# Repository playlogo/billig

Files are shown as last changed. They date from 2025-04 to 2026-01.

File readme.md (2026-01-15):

# Billig - A 3D printer from scratch

Flyby

> *Designing a 3D printer from scratch in 5 days*

**Bom**: [Google sheets](https://docs.google.com/spreadsheets/d/1451xPwitG2cd0BywjLuyT1Flae_F1tCVU7JKSqZtRoc/edit?usp=sharing)  
**CAD**: [Onshape](https://cad.onshape.com/documents/d0a1f0aa5ccbfda89a60ed00/w/724bd13dc87be16ac72aafeb/e/c63896b50a2324a549602fe6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)

About the printer:

- 440x230x200mm printing volume
- 940x410x465mm frame
- Reuses a lot of parts from two "broken" [Anycubic Kobra 2 Neos](https://de.anycubic.com/products/kobra-2-neo)
- Direct drive extruder & dual 5020 part cooling
- Completely enclosed electronics
- Build-in ABL
- With a rpi zero & Klipper-Ready
- ~$500 (including the two broken printers)

Take a look at the [Journal (has lot's of pictures!)](JOURNAL.md), the [Design notes](notes.md) or the [custom PCB (that didn't make it)](pcb/readme.md)!

Note: The stls in `printer/stls/` are only for my reference, export & download the latest ones form Onshape!

## Roadmap

Use Elecrow 7.0" Esp32 Touch display as an interface for klipper.

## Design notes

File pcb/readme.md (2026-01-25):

# Kontakt - Fan & LED control board

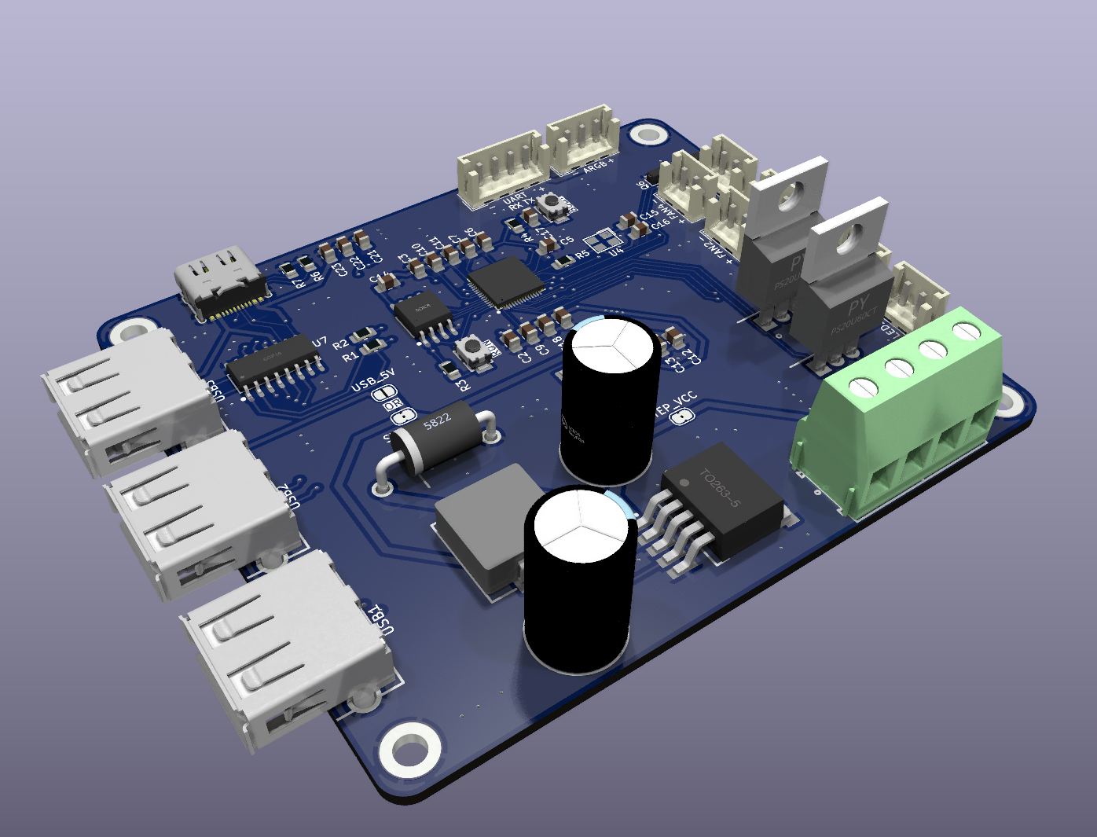
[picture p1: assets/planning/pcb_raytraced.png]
PCB routing
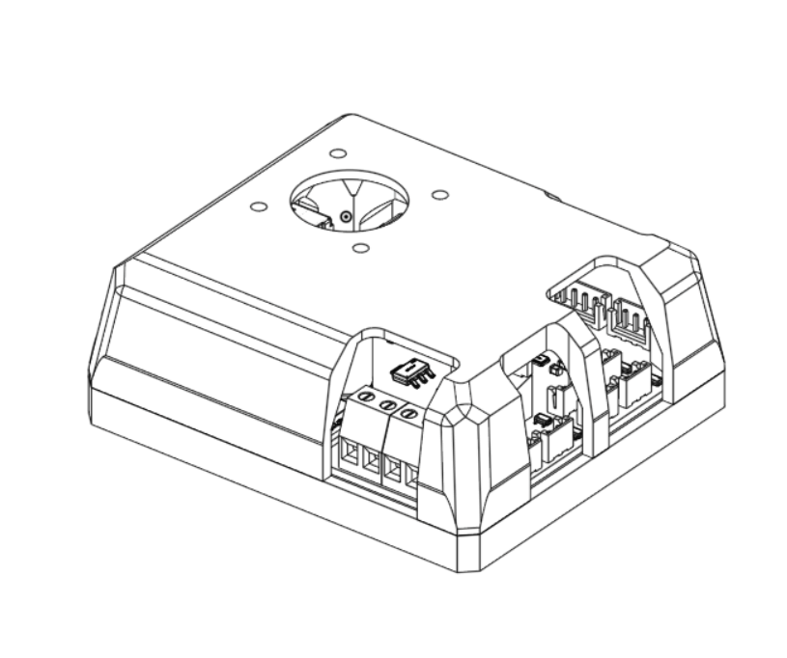
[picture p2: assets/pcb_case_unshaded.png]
PCB components
|  | |
| ---|---|
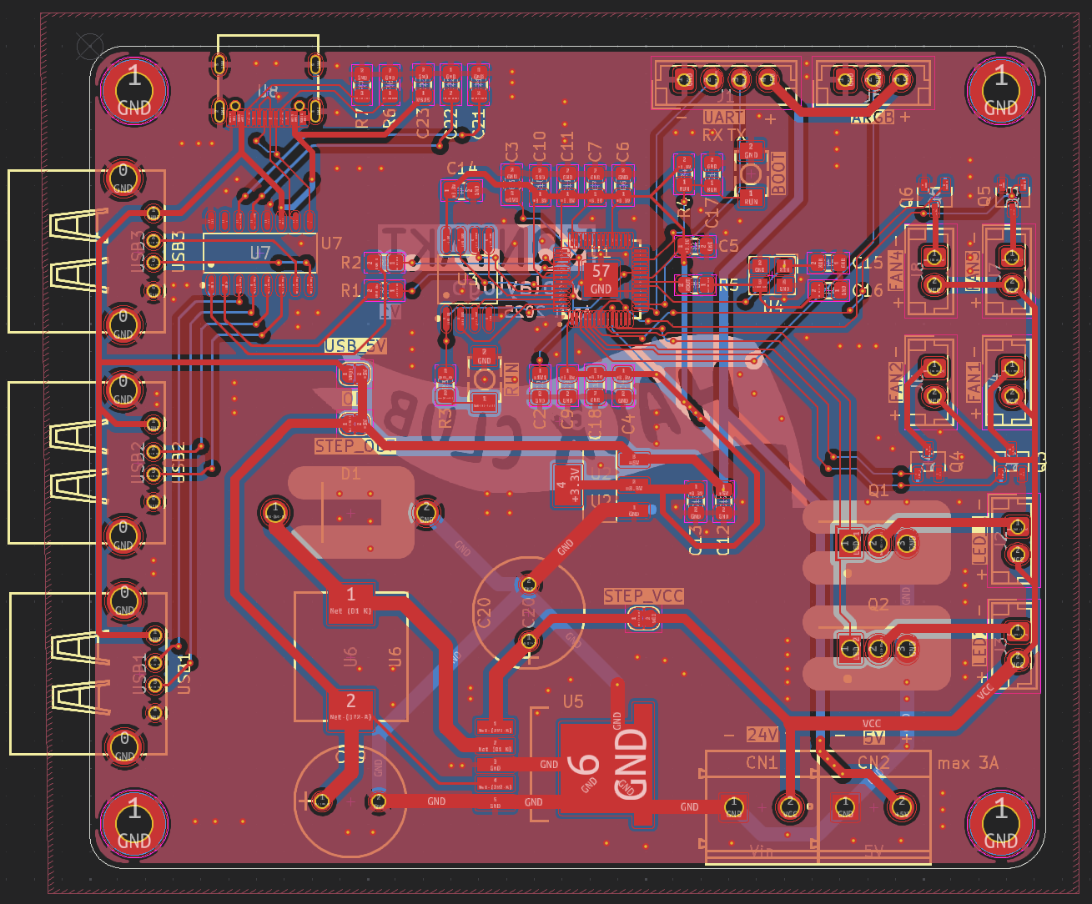
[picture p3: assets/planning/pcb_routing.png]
Case render
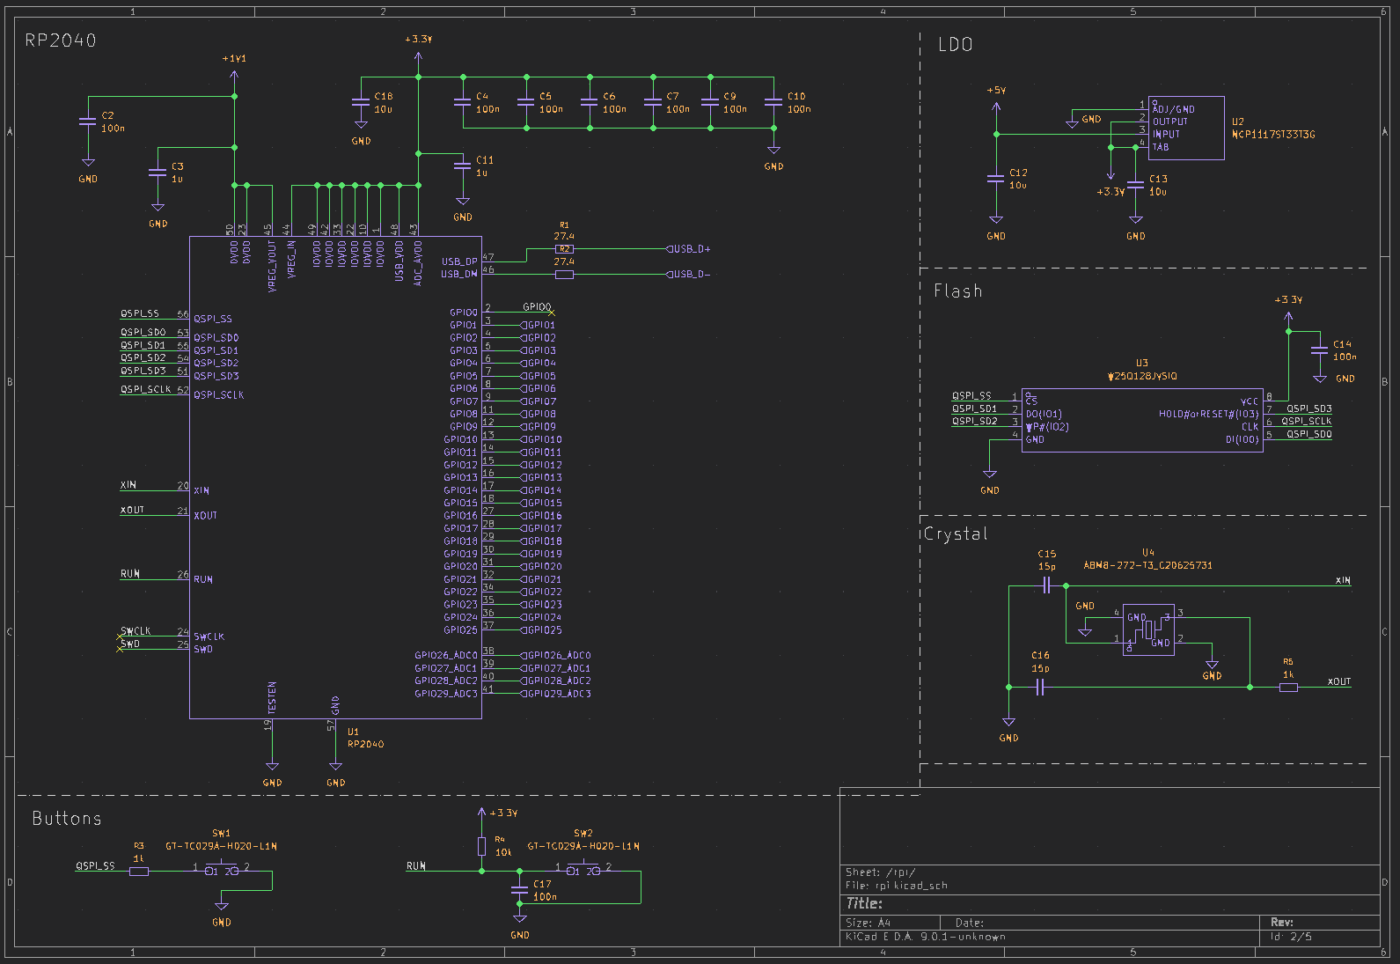
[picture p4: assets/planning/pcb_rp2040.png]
Case side view
|  |  |

Features:

- 24V power input
- Build-in 5V 3A Stepdown (for RP2040 and external RPI)
- RP2040 with 128MB Flash
- 3 Port USB hub
- 1x UART connection
- 1x ARGB connection
- 2x High current 24V PWM outputs (5A)
- 4x Low current 24V PWM outputs (2A)
- [A 3D printable case](case/) with an included 30mm fan, can be mounted to a DIN rail with [this adapter](https://www.printables.com/model/259120-horizontal-ssr-din-rail-mount/files)

Why ?: I originally only wanted to slap a rpi pico onto a pcb and add 6 mosfets to it, but like you can see I got sidetracked and added my own rp2040 (my first one!), a step-down converter (also a first) and a USB hub...

It'll be used to control the fans inside the electronics enclosure and connect the 2 control boards to the one usb port of the RPI Zero 2w, which it will also power. The high current PWM outputs are for eventual LED bar upgrades, which might or might not happen.

Firmware: I'll be using Klipper on the RP2040 with [this extension module](https://github.com/julianschill/klipper-led_effect) to control the Neopixel

Schematic: [Here](../files/schematic.pdf)

Libraries:

- [easyeda2kicad](https://github.com/uPesy/easyeda2kicad.py), needs to be installed separately, used for downloading LCSC schematics & footprints
  - Run `easyeda2kicad --full --lcsc_id=<id>` to download each component (one-by-one, yes...)

## Components

LCSC IDs:

- C2040 - RP2040
- C26537 - LDO
- C778164 - 2x Button
- C113767 - SPI Flash
- C20625731 - Crystal
- C7429053 - High current mosfet
- C5364313 - Low current mosfet
- C10002 - LM2596 3A Step down - [datasheet](https://www.lcsc.com/datasheet/lcsc_datasheet_2410010301_Texas-Instruments-LM2596SX-5-0-NOPB_C10002.pdf)
  - L1: 47uH L39 - C7529419
  - Cout: 330uF/35V - C242140
  - D1: C7503125
  - Cin: 680uF/35V - C178718
- C2915639 - Screw terminal
- C2988369 - USB C Female connector
- C192893 - USB Hub chip
- C503996 - USB Female plug

Resistors & Capacitors

- 10K C5140188
- 5.1k C26023
- 1k C17513
- 27.4ohm C2079437

- 100nF C29926
- 1uF C541528
- 10uF C1713
- 15pF C5186731

## BOM

### Parts

> Note: This is my first time soldering a rp2040 (QFN-* package in general) :D

| LCSC ID | Name | Amount |
|---|---|---|
| C2040 | RP2040 | 1x |
| C26537 | LDO | MOQ (5) |
| C778164 | 2x Button | MOQ (5) |
| C113767 | SPI Flash | 1x |
| C20625731 | Crystal | 1x |
| C7429053  | High current mosfet | 2x |
| C5364313  | Low current mosfet | MOQ(10) |
| C10002 | LM2596 3A Step down | 1x |
| C7529419  | LM2596 3A Step down (L1) | 1x |
| C242140 | LM2596 3A Step down (Cout) | MOQ (5) |
| C7503125  | LM2596 3A Step down (D1) | MOQ (5) |
| C178718 | LM2596 3A Step down (Cin) | 1x |
| C2915639  | Screw terminal | MOQ (5) |
| C2988369  | USB C Female connector | MOQ (5) |
| C192893 | USB Hub chip | MOQ (5) |
| C503996 | USB Female plug | MOQ (10) |
| C5140188  | 10K | MOQ (100) |
| C26023 | 5.1k | MOQ (100) |
| C17513 | 1k | MOQ (100) |
| C2079437  | 27.4ohm | MOQ(50) |  
| C29926 | 100nF | MOQ(50) |
| C541528 | 1uF | MOQ(50) |
| C1713 | 10uF | MOQ(20) |
| C5186731  | 15pF | MOQ(100) |

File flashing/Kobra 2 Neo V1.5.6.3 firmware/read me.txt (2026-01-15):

Update steps:
1. Format the TF card, copy the Motherboard firmware (firmware.bin) to the root directory of the TF card, and only store this file in the TF card.

2. Insert the TF card into the printer in the shutdown state, and then turn on the printer.

3. Wait for a while, and automatically update the firmware in the black screen state.

4. After the update is completed, the screen will appear  “Anycubic LOGO”, and then automatically enter the main interface. Then shut down and pull out the SD card. update completed.

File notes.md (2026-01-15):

# Design notes

Contents:

- [Filament holder](#filament-holder)
- [Bed mount](#bed-mount)
- [Frame - Bottom corner pieces](#frame---bottom-corner-pieces)
- [Frame - TPU feet](#frame---tpu-feet)
- [Motion - Endstops](#motion---endstops)
- [Frame - Z-Lead screw bottom assembly](#frame---z-leadscrew-bottom-mount)
- [BOM - Screws etc](#bom---screws-etc)
- [BOM - Reuse of parts from Kobras](#bom---reuse-of-parts-from-kobras)
- [Electronics - Mains wiring](#electronics---mains-wiring)
- [Electronics - 2 MBs](#electronics---2-controller-boards--mbs)
- [Electronics - Toolhead breakout board](#electronics---toolhead-breakout-board)
- [Electronics - Original screen](#electronics---original-screen)

## Filament holder

I'll reuse the original "Filament clip-on holder". I've added a PTFE tube mount to the top of the printer to guide the filament over the top edge and into the printing area:

*I'll add a leftover PTFE tube to the purple section*

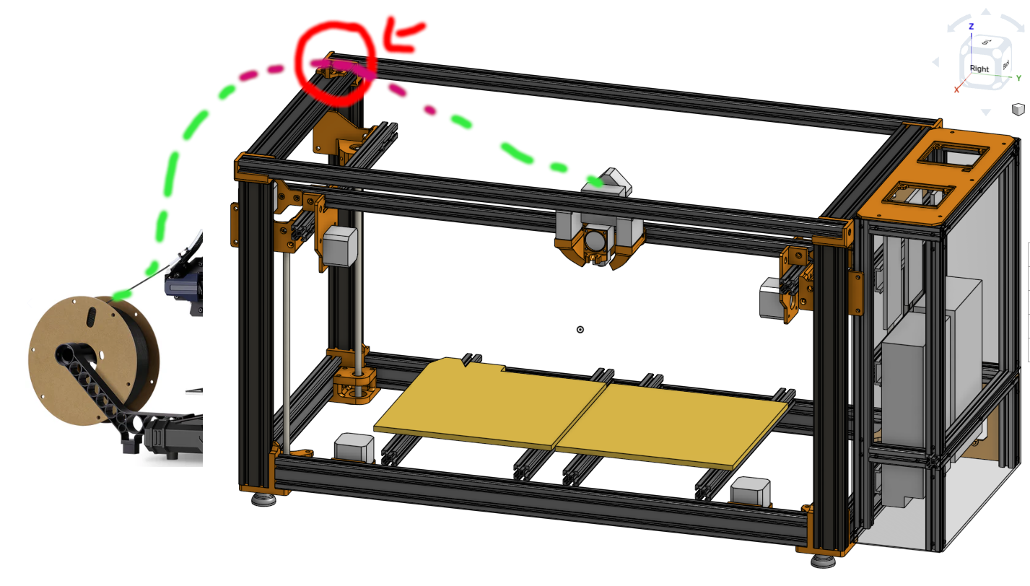
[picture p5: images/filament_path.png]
Filament path


## Bed mount

The two heatbeds will be mounted to the vertical aluminum extrusions using the silicon bed spacers, and the vertical extrusions will be mounted to the frame using these 90deg brackets (inspired by the voron 2.4 bed mount, since it can hold the sold aluminum bed, it should be strong enough to hold the cheap pcb heatbed)

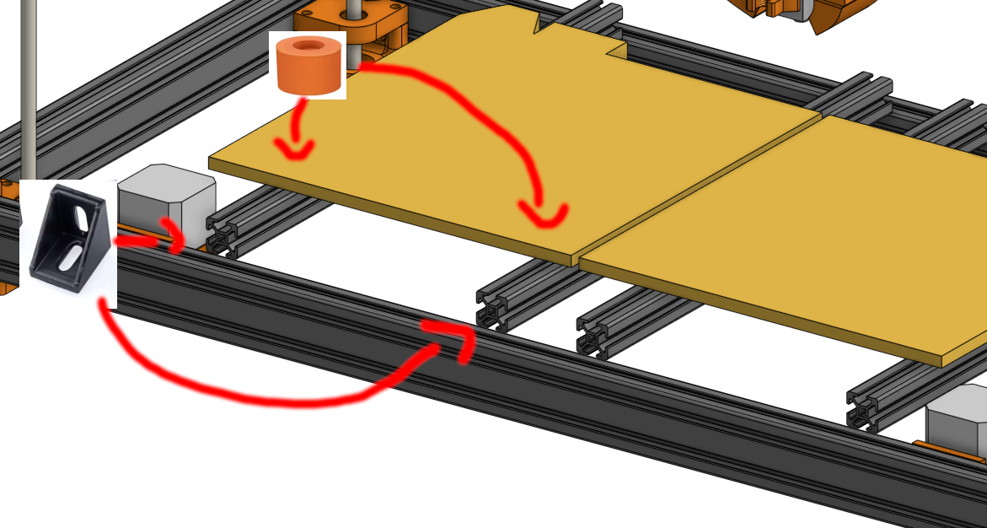
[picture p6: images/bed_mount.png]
Bed mount


## Frame - Bottom corner pieces

The aluminum extrusions will be mounted to the corner pieces using [blind joints](https://docs.vzbot.org/assets/images/manual/blind-joints/blind-joints.png). Additionally the vertical extrusions are being reused from the Kobra printers, and "slide" into the corner pieces (see picture).

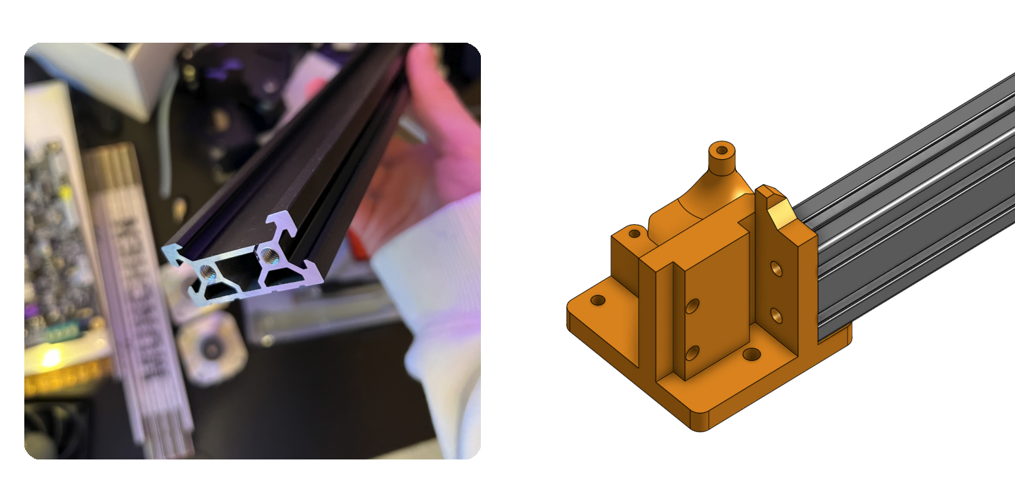
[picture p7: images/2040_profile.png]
2040 Profile


## Frame - TPU feet

The feet will be printed with TPU to be flexible and absorb *some* of the vibrations. They'll be screwed into the bottom corner pieces using M5 Screws

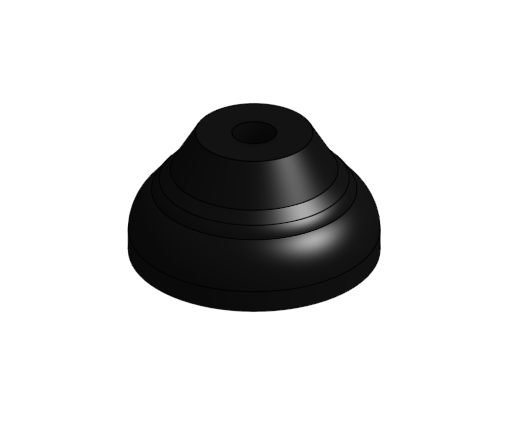
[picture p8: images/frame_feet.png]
Feet


## Motion - Endstops

I'll use microswitches as X and dual Y endstops. The Z-Axis will use the ABL sensor. Since I didn't find any accurate measurements of the microswitches, I made the "activator/clicker" (marked in green) a separate part to be easelly modified.

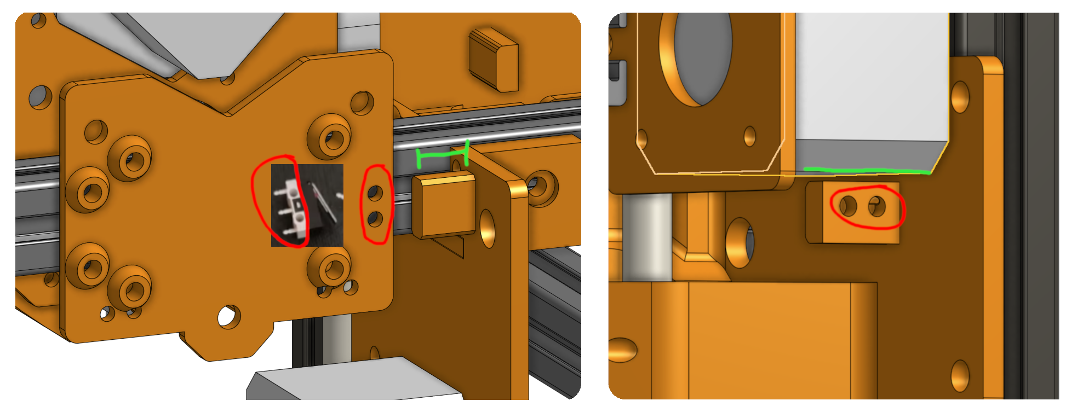
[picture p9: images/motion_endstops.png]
Endstops


## Frame - Z-Leadscrew bottom mount

Stackup of the bottom assembly:

- Printed top-cover part
- 608 barring
- Printed Spacer
- GT 40T pulley
- 608 barring
- Printed bottom part

## BOM - Screws, etc

I have various screws and other stuff left over from the two Kobra printers and the Ender3NG I just build. The BOM only contains the fasteners I'm personally missing to build the printer, not all the required ones to build it from scratch!

## BOM - Reuse of parts from Kobras

This printer reuses various parts from the two Anycubic Kobras. Most notably:

- Heatbeds & Buildplate
- PSUs, MBs, Motors, some Belts, Leadscrew
- Direct drive extruder, Hotend, ABL probe, Wires
- Some aluminum extrusions (all the darker ones in the CAD model are reused)

I **do not** reuse:

- Metal structural parts (plates, etc)
- Plastic structural parts

All orange parts in the CAD modal are self designed and will be 3D printed!

## Electronics - Mains wiring

I'll reuse the mains cable socket with buildin fuse from one of the kobras. I'll then use [this thing:5018395](https://www.thingiverse.com/thing:5018395) to mount 3 Wago 221 connectors to split the incomming mains for the two PSUs.

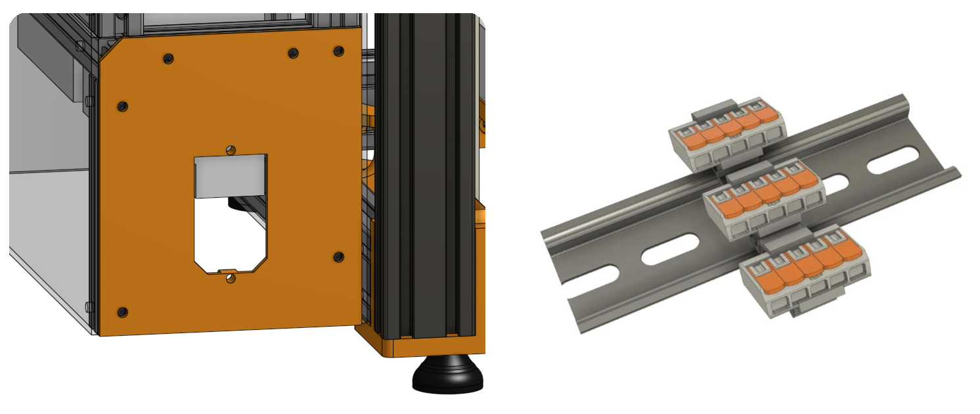
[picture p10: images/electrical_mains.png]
Mains plug & Wago holder


Each PSU will power one MB, and the right PSU will also be connected to this [step down converter](https://de.aliexpress.com/item/1005007820952595.html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) to produce 5V for the rpi zero.

## Electronics - 2 Controller boards / MBs

Since this printer uses two Control boards (MBs) with only 4 stepper drivers each I need to split the 6 steppers between them.

The first board will only control the two Z-Steppers and one heatbed.  
The second board will control the two Y-Steppers, the one X-Stepper, the extruder, the hotend and one heatbed.

This shouldn't cause any problems, since the Z-Axis is the slowest and least used axis, and any possible delay between the two MBs shouldn't really matter.

I'll cut holes and slots into the acrylic backplate to make place for the stepper motor, etc. cables.

## Electronics - Toolhead breakout board

I'll reuse the original toolhead breakout board and mount it to the new toolhead. The breakout board connects the ABL probe, heater,  thermistor, fans and extruder stepper using a 18-Pin IDC cable to the MBs.

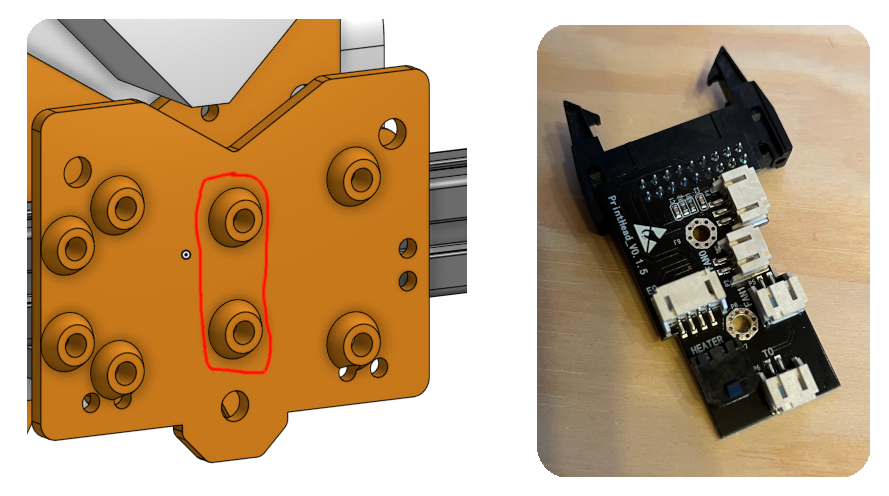
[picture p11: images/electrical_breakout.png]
Breakout board


## Electronics - Original screen

Connect original screen to an ESP32. Apparently it's a 2.4" SPI screen with the ILI9341 controller.

- [Reddit post with pinout](https://www.reddit.com/r/klippers/comments/1e7ab61/wip_kobra_2_neo_esp32_vnc_klipperscreen/)
- [Firmware for an ESP32 to display a VNC](https://github.com/DakillerV/Esp32TFTVNC/tree/main)
- [KlipperScreen config & pinout (direct rpi hookup)](https://github.com/cheadrian/kobra2neo-klipper/tree/main/KlipperScreen)

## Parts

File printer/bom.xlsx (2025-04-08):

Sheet: BOM
Name | Amount | Price | Link | Note |  | Total
Electronics |  |  |  |  |  | €18.68
DIN rail | 3 | €1.89 | Aliexpress (https://de.aliexpress.com/item/1005001553239891.html?utparam-url=scene:search%7Cquery_from:) | 30cm |  | €5.67
ADXL345 | 1 | €1.79 | Aliexpress (https://de.aliexpress.com/item/1005006160667610.html?utparam-url=scene%3Asearch%7Cquery_from%3A) |  |  | €1.79
5V step down | 1 | €3.39 | Aliexpress (https://de.aliexpress.com/item/1005007820952595.html) |  |  | €3.39
JST-PH 3-Pin cable | 1 | €2.05 | Aliexpress (https://de.aliexpress.com/item/1005004792920714.html?mp=1) | 3p, 20cm |  | €2.05
Molex Micro-fit 3 Female cable - 2 Pin | 1 | €5.78 | Aliexpress (https://de.aliexpress.com/item/1005005748828197.html?mp=1) | Female, 2P - 1.79€ per + 3.28€ shipping |  | €5.78
Molex Micro-fit 3 Male cable - 2 Pin | 1 | €0.00 | (same as above) | Male, 2P - 1.79€ per + 0€ shipping -> combined into price above |  | €0.00
Motion |  |  |  |  |  | €37.75
Microswitch | 1 | €1.29 | Aliexpress (https://de.aliexpress.com/item/1005005596552328.html?scm_id=1007.40050.354490.0&scm-url=1007.40050.354490.0) | Handle 11.5mm |  | €1.29
Z Leadscrew | 2 | €5.59 | Aliexpress (https://de.aliexpress.com/item/32435304660.html?scm_id=1007.40050.354490.0&scm-url=1007.40050.354490.0) | 330mm |  | €11.18
Anti-backlash nut | 4 | €1.69 | Aliexpress (https://de.aliexpress.com/item/1005006176710464.html?scm_id=1007.40050.354490.0&scm-url=1007.40050.354490.0) | Lead 8mm |  | €6.76
GT2 Pulley 40T | 4 | €1.65 | Aliexpress (https://de.aliexpress.com/item/32880112920.html?scm_id=1007.40050.354490.0&scm-url=1007.40050.354490.0) | 40T 8mm |  | €6.60
GT2 Pulley 20T | 1 | €2.84 | Aliexpress (https://de.aliexpress.com/item/1005005979956097.html?scm_id=1007.40050.354490.0&scm-url=1007.40050.354490.0) | 20T W6 B5, 5pcs |  | €2.84
608 RS bearing | 1 | €2.85 | Aliexpress (https://de.aliexpress.com/item/1005005802947436.html) | 10pcs |  | €2.85
GT2 6mm Closed loop | 2 | €2.09 | Aliexpress (https://de.aliexpress.com/item/1005004113657502.html?scm_id=1007.40050.354490.0&scm-url=1007.40050.354490.0) | 2GT-782, Belt Width 6mm 1pcs |  | €4.18
GT2 6mm Open belt | 1 | €2.05 | Aliexpress (https://de.aliexpress.com/item/32970768914.html?scm_id=1007.40050.354490.0&scm-url=1007.40050.354490.0) | 2m, A type |  | €2.05
Heated Bed |  |  |  |  |  | €8.76
Heatbed insulator | 2 | €1.69 | Aliexpress (https://de.aliexpress.com/item/32969500959.html) | 235x235mm |  | €3.38
Silicone spacers | 2 | €2.69 | Aliexpress (https://de.aliexpress.com/item/1005007438124730.html?utparam-url=scene:search%7Cquery_from:) | 4pcs Brown 12mm |  | €5.38
Frame |  |  |  |  |  | €85.73
90deg side mount | 1 | €5.19 | Aliexpress (https://de.aliexpress.com/item/1005007297685965.html?scm_id=1007.40050.354490.0&scm-url=1007.40050.354490.0) | 20pcs |  | €5.19
2020 I-Type Nut 5 - 800mm | 2 | €6.02 | Dolt mechatronik (https://www.dold-mechatronik.de/Aluminum-Profile-Black-20x20L-I-Type-Groove-5-049kg-m-Customized-Cutting-50-to-6000mm) |  |  | €12.04
2020 I-Type Nut 5 - 386mm | 2 | €3.11 | Dolt mechatronik (https://www.dold-mechatronik.de/Aluminum-Profile-Black-20x20L-I-Type-Groove-5-049kg-m-Customized-Cutting-50-to-6000mm) |  |  | €6.22
2020 I-Type Nut 5 - 728mm | 1 | €5.52 | Dolt mechatronik (https://www.dold-mechatronik.de/Aluminum-Profile-Black-20x20L-I-Type-Groove-5-049kg-m-Customized-Cutting-50-to-6000mm) |  |  | €5.52
2020 I-Type Nut 5 - 361mm | 2 | €2.94 | Dolt mechatronik (https://www.dold-mechatronik.de/Aluminum-Profile-Black-20x20L-I-Type-Groove-5-049kg-m-Customized-Cutting-50-to-6000mm) |  | +2x 3D printered adapter to use profile from Kobra | €5.88
2020 I-Type Nut 5 - 418mm | 2 | €3.38 | Dolt mechatronik (https://www.dold-mechatronik.de/Aluminum-Profile-Black-20x20L-I-Type-Groove-5-049kg-m-Customized-Cutting-50-to-6000mm) | electronics enclosure |  | €6.76
2020 I-Type Nut 5 - 291mm | 4 | €2.46 | Dolt mechatronik (https://www.dold-mechatronik.de/Aluminum-Profile-Black-20x20L-I-Type-Groove-5-049kg-m-Customized-Cutting-50-to-6000mm) | electronics enclosure |  | €9.84
2020 I-Type Nut 5 - 110mm | 0 | €1.23 | Dolt mechatronik (https://www.dold-mechatronik.de/Aluminum-Profile-Black-20x20L-I-Type-Groove-5-049kg-m-Customized-Cutting-50-to-6000mm) | electronics enclosure | 2x 3D print instead | €0.00
2020 I-Type Nut 5 - 288mm | 2 | €2.44 | Dolt mechatronik (https://www.dold-mechatronik.de/Aluminum-Profile-Black-20x20L-I-Type-Groove-5-049kg-m-Customized-Cutting-50-to-6000mm) | electronics enclosure |  | €4.88
2020 I-Type Nut 5 - 94.5 | 0 | €1.12 | Dolt mechatronik (https://www.dold-mechatronik.de/Aluminum-Profile-Black-20x20L-I-Type-Groove-5-049kg-m-Customized-Cutting-50-to-6000mm) | electronics enclosure | 2x 3D print instead | €0.00
2020 I-Type Nut 5 - 74.5mm | 0 | €0.98 | Dolt mechatronik (https://www.dold-mechatronik.de/Aluminum-Profile-Black-20x20L-I-Type-Groove-5-049kg-m-Customized-Cutting-50-to-6000mm) | electronics enclosure | 2x 3D print instead | €0.00
2020 I-Type Nut 5 - 331mm | 1 | €2.78 | Dolt mechatronik (https://www.dold-mechatronik.de/Aluminum-Profile-Black-20x20L-I-Type-Groove-5-049kg-m-Customized-Cutting-50-to-6000mm) | electronics enclosure |  | €2.78
2040 I-Type Nut 5 - 345mm | 2 | €4.54 | Dolt mechatronik (https://www.dold-mechatronik.de/Aluminum-Profile-Black-20x20L-I-Type-Groove-5-049kg-m-Customized-Cutting-50-to-6000mm) |  |  | €9.08
2040 I-Type Nut 5 - 704mm | 2 | €8.77 | Dolt mechatronik (https://www.dold-mechatronik.de/Aluminum-Profile-Black-20x20L-I-Type-Groove-5-049kg-m-Customized-Cutting-50-to-6000mm) |  |  | €17.54
Plexiglass |  |  |  |  |  | €17.95
Makrolon® UV 2760 grau 3mm | 1 | €8.53 | Acrylics (https://acrylglas-shop.com/makrolon-uv-2760-grau-3mm) | 438x331mm |  | €8.53
Acrylglas XT Stärke 3 mm farblos | 1 | €2.05 | Acrylics (https://acrylglas-shop.com/acrylglas-xt-staerke-3-mm-farblos) | 114.5x438mm |  | €2.05
Acrylglas XT Stärke 3 mm farblos | 1 | €4.17 | Acrylics (https://acrylglas-shop.com/acrylglas-xt-staerke-3-mm-farblos) | 331x308mm |  | €4.17
Acrylglas XT Stärke 3 mm farblos | 1 | €1.76 | Acrylics (https://acrylglas-shop.com/acrylglas-xt-staerke-3-mm-farblos) | 331x130mm |  | €1.76
Acrylglas XT Stärke 3 mm farblos | 1 | €1.44 | Acrylics (https://acrylglas-shop.com/acrylglas-xt-staerke-3-mm-farblos) | 114.5x308mm |  | €1.44
Fasteners |  |  |  |  |  | €38.42
Heat insert - M6 | 1 | €2.79 | Aliexpress (https://de.aliexpress.com/item/1005003582355741.html?utparam-url=scene:search%7Cquery_from:) | M6 (OD=8), 6mm 30pcs |  | €2.79
Heat insert - M4 | 1 | €3.09 | Aliexpress (https://de.aliexpress.com/item/1005006071488810.html) | M4xL5xOD6, 30pcs |  | €3.09
Spacer - M5 | 1 | €2.05 | Aliexpress (https://de.aliexpress.com/item/1005006448473041.html) | M5 x 10 x 1(50pcs) |  | €2.05
Hex-outside-socket screw - M5 16mm | 2 | €1.90 | Aliexpress (https://de.aliexpress.com/item/32810852732.html?utparam-url=scene%3Asearch%7Cquery_from%3A) | M5 10pcs, 16mm, 304 stainless steel |  | €3.80
Hex-outside-socket screw - M4 14mm | 1 | €2.06 | Aliexpress (https://de.aliexpress.com/item/32810852732.html?utparam-url=scene%3Asearch%7Cquery_from%3A) | M4 20pcs, 14mm, 304 stainless steel |  | €2.06
Hex-head screw - M5 12mm | 2 | €1.83 | Aliexpress (https://de.aliexpress.com/item/32810872544.html?utparam-url=scene%3Asearch%7Cquery_from%3A) | M5 10pcs, 12mm, 12.9 Class steel |  | €3.66
Hex-head screw - M4 12mm | 1 | €1.98 | Aliexpress (https://de.aliexpress.com/item/32810872544.html?utparam-url=scene%3Asearch%7Cquery_from%3A) | M4 20pcs, 12mm, 12.9 Class steel |  | €1.98
Hex-head-screw - M4 8mm | 2 | €1.72 | Aliexpress (https://de.aliexpress.com/item/32810872544.html?utparam-url=scene%3Asearch%7Cquery_from%3A) | M20pcs, 8mm, 12.9 Class steel |  | €3.44
Hex-head screw - M3 14mm | 1 | €2.23 | Aliexpress (https://de.aliexpress.com/item/32810872544.html?utparam-url=scene%3Asearch%7Cquery_from%3A) | M3 50pcs, 14mm, 12.9 Class steel |  | €2.23
Hex-head screw - M3 8mm | 1 | €1.61 | Aliexpress (https://de.aliexpress.com/item/32810872544.html?utparam-url=scene%3Asearch%7Cquery_from%3A) | M3 50pcs, 8mm, 12.9 Class steel |  | €1.61
Hex-socket screw - M4 50mm | 1 | €3.35 | Aliexpress (https://de.aliexpress.com/item/1005007798633538.html?utparam-url=scene%3Asearch%7Cquery_from%3A) | M4 (25pcs), 50mm |  | €3.35
Hex-socket screw - M4 12mm | 1 | €1.49 | Aliexpress (https://de.aliexpress.com/item/1005007798633538.html?utparam-url=scene%3Asearch%7Cquery_from%3A) | M4 (25pcs), 12mm |  | €1.49
Hex-socket screw - M3 6mm | 1 | €1.45 | Aliexpress (https://de.aliexpress.com/item/1005007798633538.html?utparam-url=scene%3Asearch%7Cquery_from%3A) | M3 (55pcs), 6mm |  | €1.45
T-Nut - M4 *strong type* | 1 | €3.19 | Aliexpress (https://de.aliexpress.com/item/32964780472.html?utparam-url=scene%3Asearch%7Cquery_from%3A) | 2020-M4-50PCS |  | €3.19
T-Nut - M4 *weak type* | 1 | €2.23 | Aliexpress (https://de.aliexpress.com/item/32814359094.html?scm_id=1007.40050.354490.0&scm-url=1007.40050.354490.0) | M4 - 50pcs |  | €2.23
Misc |  |  |  |  |  | €9.90
Aliexpress coupons | 1 | -€6.00 |  |  |  | -€6.00
Shipping - Aluprofile Express | 1 | €5.95 |  |  |  | €5.95
Shipping - Acrylics | 1 | €9.95 |  |  |  | €9.95
 |  |  |  |  | Total | €217.19
 |  |  |  |  | + 2 Anycubic Kobra 2 Neo Priners: 94.98 | €312.17 | ~ | $340.27

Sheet: legacy_without kobras
Name | Amount | Price | Link | Note |  | Total
Electronics |  |  |  |  |  | €77.87
BTT SKR Mini E3 | 1 | €25.00 | Aliexpress (https://de.aliexpress.com/item/1005006042517491.html?utparam-url=scene%3Asearch%7Cquery_from%3A) | One for X/Y/E/Bed1, Second one for Z1/Z2/Bed2 | Prefer second one over External mosfet | €25.00
Meanwell 24V 14.6A PSU | 2 | €22.29 | Stepper online (https://www.omc-stepperonline.com/de/lrs-350-24-mean-well-350w-24vdc-14-6a-115-230vac-geschlossenes-schaltnetzteil-lrs-350-24) | SKRs on seperate circuits |  | €44.58
External Mosfet | 0 | €2.00 | Aliexpress (https://de.aliexpress.com/item/32896175700.html?utparam-url=scene%3Asearch%7Cquery_from%3A) | 2€ in a "BundleDeal" | Maybe not as safe ? | €0.00
Better external mosfet | 1 | €8.29 | Aliexpress (https://de.aliexpress.com/item/32405884519.html?pdp_ext_f=%7B%22order%22%3A%2258%22%7D) | For Bed2 | Wayyyyy more trustworthy | €8.29
Motion |  |  |  |  |  | €103.00
3x Nema 17 x38mm | 2 | €16.00 | Stepper online (https://www.omc-stepperonline.com/de/3-stueck-e-serie-nema-17-bipolar-42-ncm-59-49-oz-in-1-5a-42x42x38mm-4-draehte-3-17he15-1504s) | X/Y/E Z1/Z2 |  | €32.00
Nema 17 x48 | 0 | €10.00 | Stepper online (https://www.omc-stepperonline.com/de/e-serie-nema-17-bipolar-59ncm-84oz-in-2a-42x48mm-4draehte-w-1m-kabel-verbinder-17he19-2004s) | Stronger X/Y ? |  | €0.00
Z linear rails | 0 | €9.00 |  |  |  | €0.00
Z Leadscrew | 4 | €3.00 |  |  |  | €12.00
GT2 6mm Closed loop | 2 | €3.00 |  |  |  | €6.00
Random belt stuff | 1 | €10.00 |  |  |  | €10.00
Z V-Wheels | 4 | €0.00 | In stock |  |  | €0.00
CoreXY Belt Open | 1 | €10.00 |  |  |  | €10.00
Belt bearings | 1 | €15.00 |  |  |  | €15.00
Y linear rails | 2 | €8.00 |  |  |  | €16.00
X V-Wheeled | 1 | €2.00 |  |  |  | €2.00
Hotend |  |  |  |  |  | €21.00
V6 clone | 1 | €4.00 | Aliexpress (https://de.aliexpress.com/item/1005003651646732.html?utparam-url=scene:search%7Cquery_from:) |  |  | €4.00
4020 axial | 1 | €2.00 |  |  |  | €2.00
4020 radial | 2 | €2.00 |  |  |  | €4.00
optical runout sensor | 1 | €3.00 |  |  |  | €3.00
Cheap bowden tube | 1 | €3.00 |  |  |  | €3.00
Cheap extruder | 1 | €5.00 |  |  |  | €5.00
Heated Bed |  |  |  |  |  | €55.36
235x235mm PCB heater /w Aluminum top | 2 | €14.99 | Aliexpress (https://de.aliexpress.com/item/1005007288279620.html) | 235x235x3mm 24V, 160W | Way to epensive, 8€ normal | €29.98
235x235mm PEI Build plate with magnetic base | 2 | €12.69 | Aliexpress (https://de.aliexpress.com/item/1005007653702685.html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) | magnetic base, 235x235mm |  | €25.38
Frame |  |  |  |  |  | €113.00
Aluminum profile | 1 | €80.00 | Aluprofile Express (https://www.aluprofile-express.de/Aluminiumprofil-schwarz-20x40L-I-Typ-Nut-5-088kg-m-Zuschnitt-50-6000mm) |  |  | €80.00
Random screws & T-Nuts | 1 | €30.00 | Aliexpress |  |  | €30.00
Aluminum profile side 90deg mount, 3d print | 1 | €3.00 | Aliexpress (https://de.aliexpress.com/item/1005004799892392.html?utparam-url=scene%3Asearch%7Cquery_from%3A) |  |  | €3.00
Misc |  |  |  |  |  | -€4.90
Shipping - Stepper online | 1 | €6.20 |  |  |  | €6.20
Aliexpress coupons | 1 | -€18.00 |  |  |  | -€18.00
Shipping - Aluprofile Express | 1 | €6.90 |  |  |  | €6.90
Should haves |  |  |  |  |  | €3.27
3D touch | 0 | €7.00 | Aliexpress (https://de.aliexpress.com/item/1005001865225039.html?utparam-url=scene:search%7Cquery_from:) |  |  | €0.00
Thermal fuse | 3 | €1.09 | Aliexpress (https://de.aliexpress.com/item/1005006900456941.html?utparam-url=scene%3Asearch%7Cquery_from%3A) | Ceramic holes-10A-NC, 75° | Solder inbetween heated bed + power, 2 extra for testing at 75° and 100° (I do not trust them) | €3.27
 |  |  |  |  | Total | €373.50

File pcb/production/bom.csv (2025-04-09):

Designator | Footprint | Quantity | Value | LCSC Part #
C10, C14, C17, C2, C4, C5, C6, C7, C9 | 0805 | 9 | 100n
C11, C3 | 0805 | 2 | 1u
C12, C13, C18 | 0805 | 3 | 10u
C15, C16 | 0805 | 2 | 15p
C19 | CAP-TH_BD10.0-P5.00-D1.0-FD | 1 | EEUEB1V331B | C242140
C20 | CAP-TH_BD10.0-P5.00-D1.0-FD | 1 | EEUFR1V681 | C178718
C21, C22, C23 | 0805 | 3 | 10uF
CN1 | CONN-TH_2P-P5.08_DIBO_DB128V-5.08 | 1 | Vin | C2915639
CN2 | CONN-TH_2P-P5.08_DIBO_DB128V-5.08 | 1 | 5V | C2915639
D1 | DO-27_BD5.3-L8.4-P12.40-D1.3-RD | 1 | 1N5824_C7503125 | C7503125
J1 | JST_EH_B4B-EH-A_1x04_P2.50mm_Vertical | 1 | UART
J2 | JST_EH_B2B-EH-A_1x02_P2.50mm_Vertical | 1 | LED_1
J3 | JST_EH_B2B-EH-A_1x02_P2.50mm_Vertical | 1 | LED2
J4 | JST_EH_B2B-EH-A_1x02_P2.50mm_Vertical | 1 | FAN1
J5 | JST_EH_B3B-EH-A_1x03_P2.50mm_Vertical | 1 | ARGB
J6 | JST_EH_B2B-EH-A_1x02_P2.50mm_Vertical | 1 | FAN2
J7 | JST_EH_B2B-EH-A_1x02_P2.50mm_Vertical | 1 | FAN3
J8 | JST_EH_B2B-EH-A_1x02_P2.50mm_Vertical | 1 | FAN4
Q1, Q2 | TO-220AB-3_L10.4-W4.6-P2.54-L | 2 | IRLB8721PBF-VB | C7429053
Q3, Q4, Q5, Q6 | SOT-23-3_L3.0-W1.7-P0.95-LS2.9-BR | 4 | IRLML6344 | C5364313
R1, R2 | 0805 | 2 | 27.4
R3, R5 | 0805 | 2 | 1k
R4 | 0805 | 1 | 10k
R6, R7 | 0805 | 2 | 5.1k
SW1, SW2 | SW-SMD_L3.9-W2.9-LS5.0 | 2 | GT-TC029A-H020-L1N | C778164
U1 | LQFN-56_L7.0-W7.0-P0.4-EP | 1 | RP2040 | C2040
U2 | SOT-223-3_L6.5-W3.4-P2.30-LS7.0-BR | 1 | NCP1117ST33T3G | C26537
U3 | SOIC-8_L5.3-W5.3-P1.27-LS8.0-BL | 1 | W25Q128JVSIQ | C113767
U4 | CRYSTAL-SMD_4P-L3.2-W2.5-BL | 1 | ABM8-272-T3_C20625731 | C20625731
U5 | TO-263-5_L10.2-W8.9-P1.70-TL | 1 | LM2596SX-5.0/NOPB | C10002
U6 | IND-SMD_L11.6-W10.1 | 1 | CYA1050-47UH | C7529419
U7 | SOP-16_L10.0-W3.9-P1.27-LS6.0-BL | 1 | SL2.1A | C192893
U8 | USB-C-SMD_G-SWITCH_GT-USB-7010ASV | 1 | GT-USB-7010ASV | C2988369
USB1, USB2, USB3 | USB-A-TH_USB-A-F-90 | 3 | KH-AF90DIP-112 | C503996

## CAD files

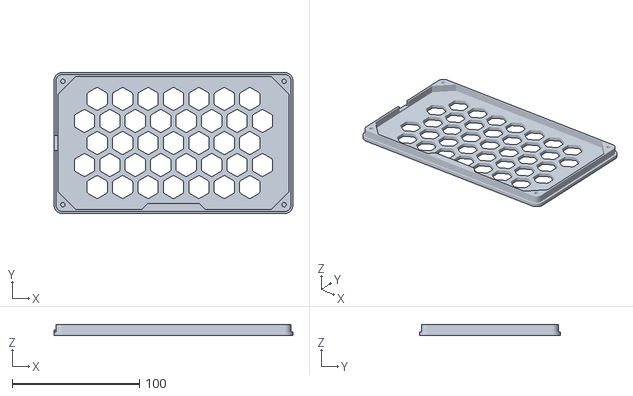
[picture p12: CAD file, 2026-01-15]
display/HMI_CASE_BOTTOM.stl
188.0 x 111.0 x 9.00

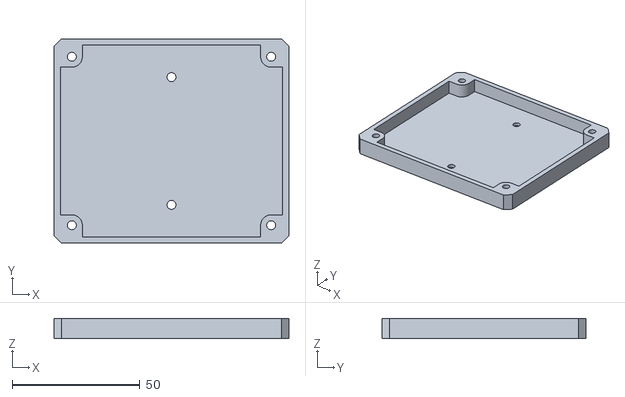
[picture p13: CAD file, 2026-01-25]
pcb/case/case_bottom.stl
92.0 x 80.0 x 8.00

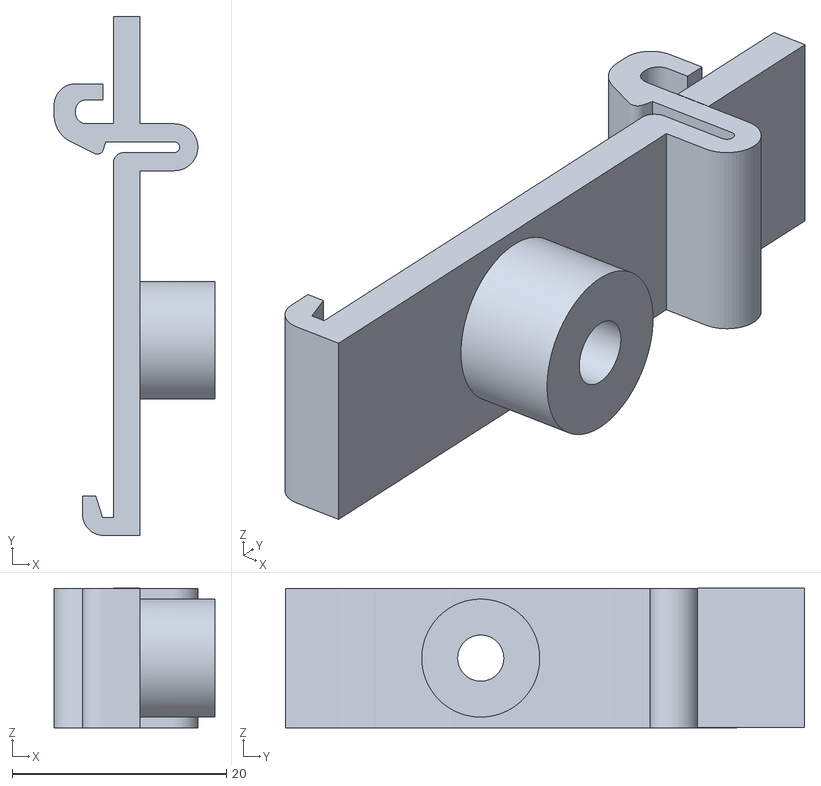
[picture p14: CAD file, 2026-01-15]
printer/stls/DIN/Billig-PSU-DIN-Clip-PSU-DIN-Clip-.stl
15.0 x 48.4 x 13.0

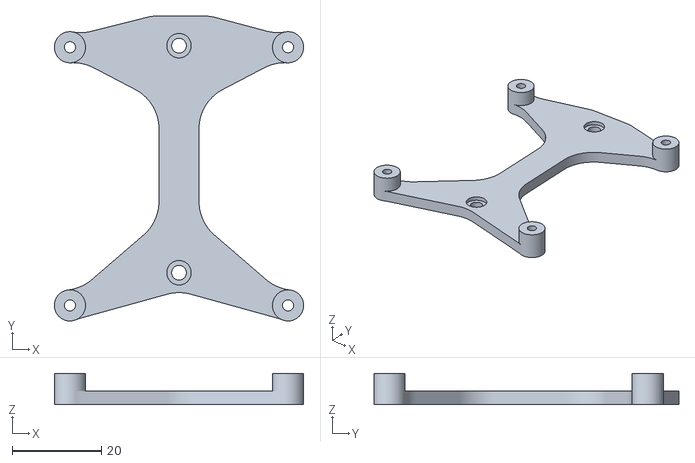
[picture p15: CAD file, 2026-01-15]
printer/stls/Electronics mount/Billig-DIN mounts-BTT-Pico-Mount-.stl
56.0 x 68.5 x 7.00

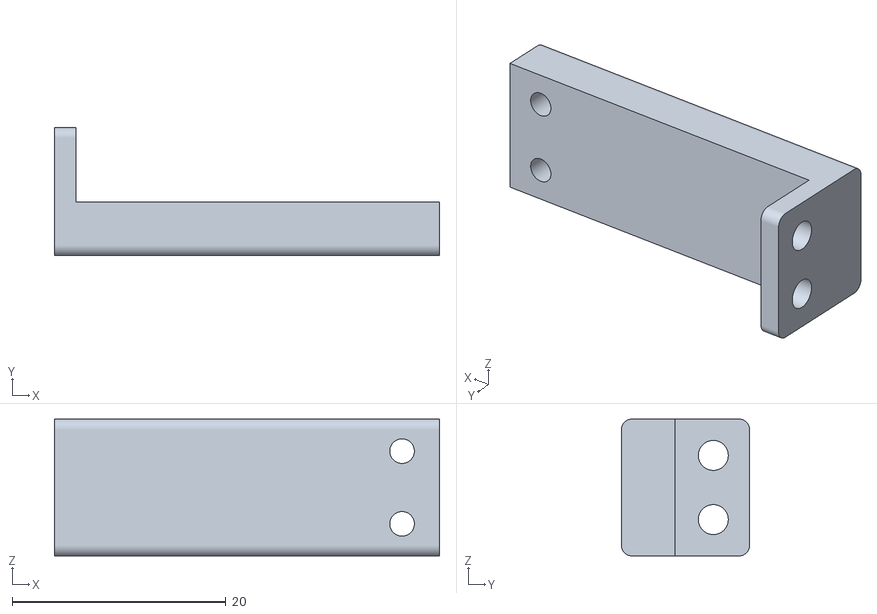
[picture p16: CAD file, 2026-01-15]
printer/stls/Endstops/Billig-Gantry-Endstop-Fix-Y-1-.stl
36.0 x 12.0 x 12.8

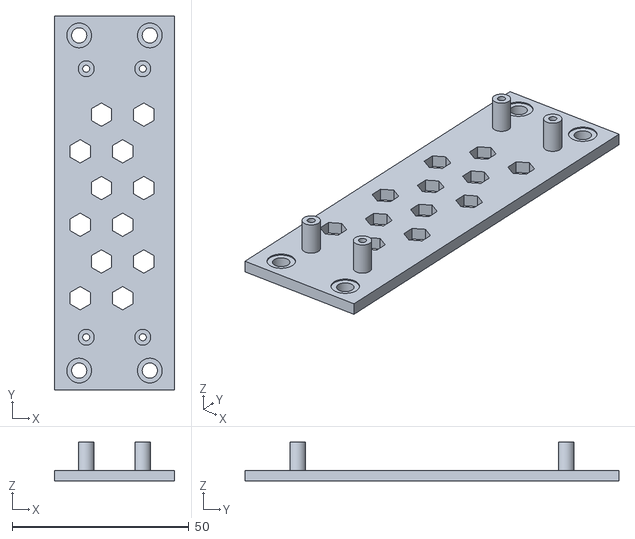
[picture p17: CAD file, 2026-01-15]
printer/stls/Extras/Billig-Random small stuff-CableExtender Bottom-.stl
34.0 x 105.9 x 11.0

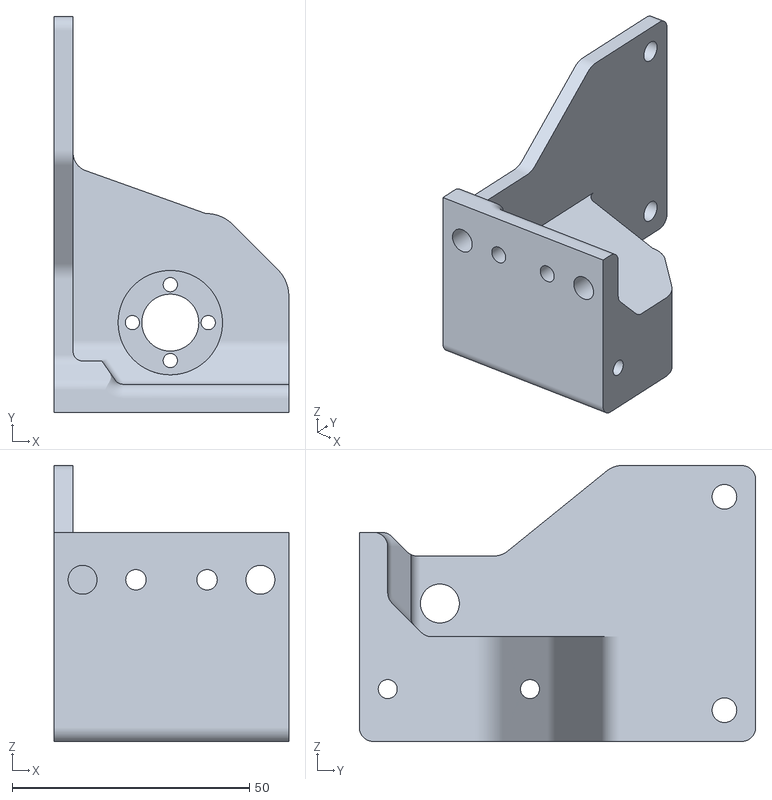
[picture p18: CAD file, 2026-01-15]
printer/stls/Fixes/BR.stl
49.5 x 83.6 x 58.2

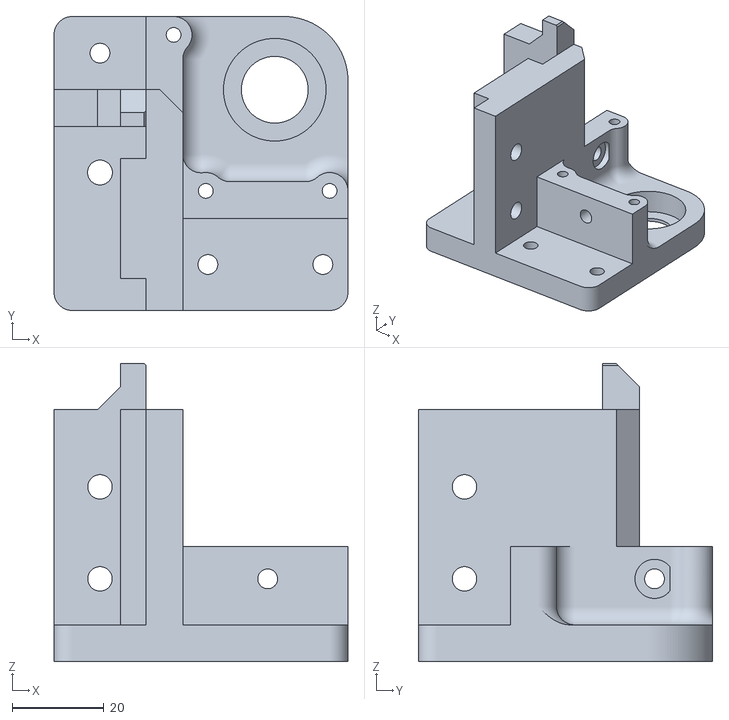
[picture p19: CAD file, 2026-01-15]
printer/stls/Frame/Frame-Corner-Bottom-LB.stl.stl
63.9 x 63.9 x 64.9

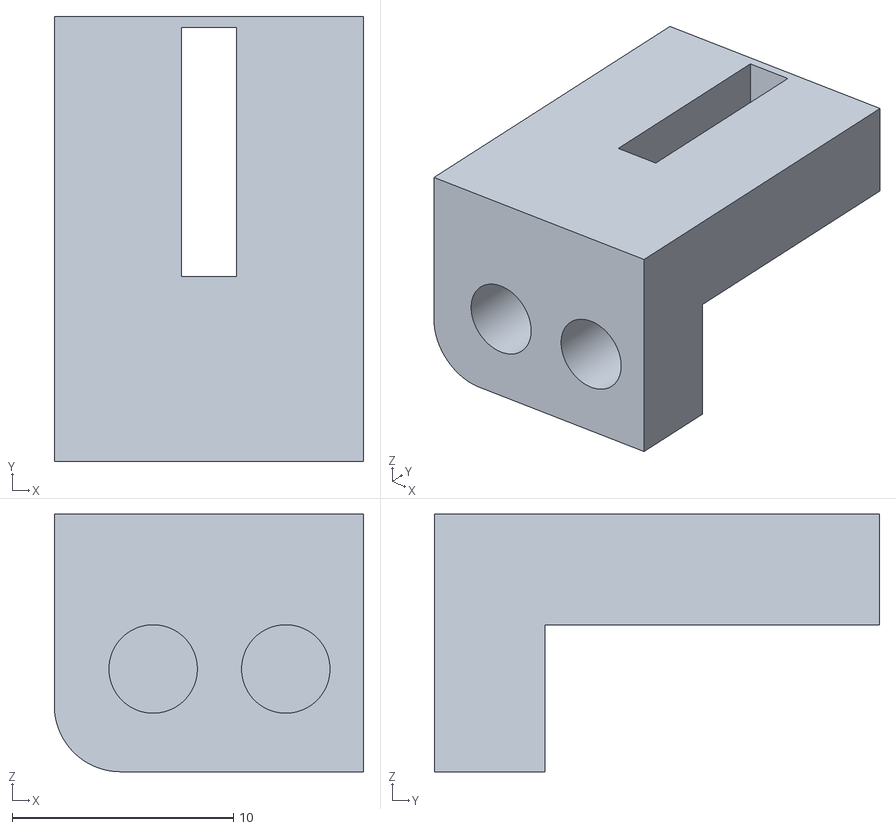
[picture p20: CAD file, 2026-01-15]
printer/stls/Toolhead/Billig-Toolhead-Belt clip-.stl
14.0 x 20.1 x 11.6

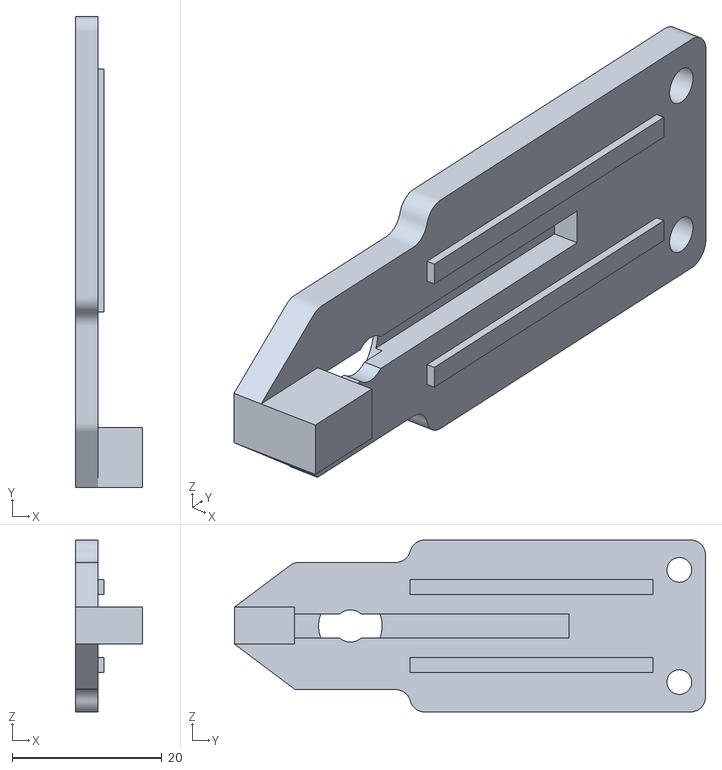
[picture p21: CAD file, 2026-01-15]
printer/stls/XY-Axis/Y-Belt-Case-2.stl
9.00 x 63.0 x 23.0

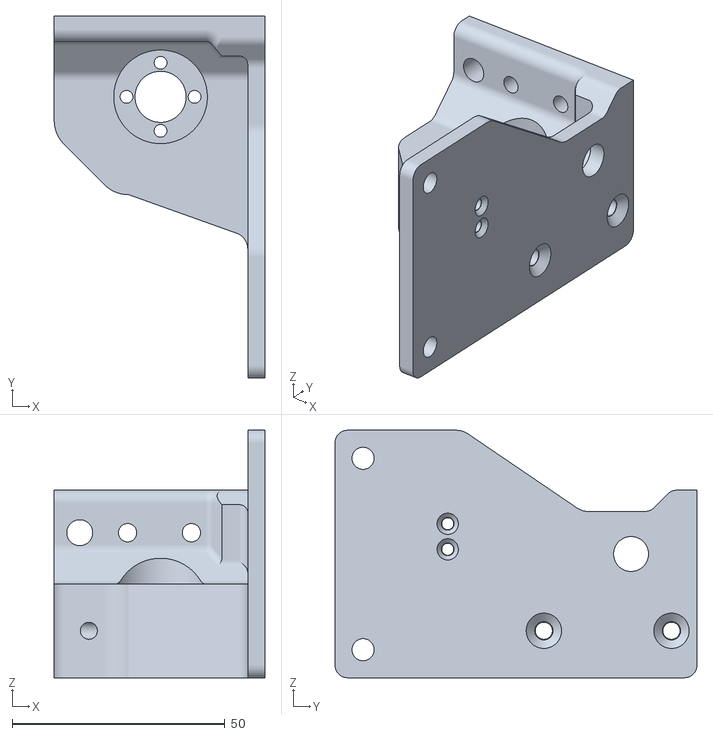
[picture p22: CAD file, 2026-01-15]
printer/stls/Z-Axis/Z-Mount-LF.stl
49.5 x 85.1 x 58.2

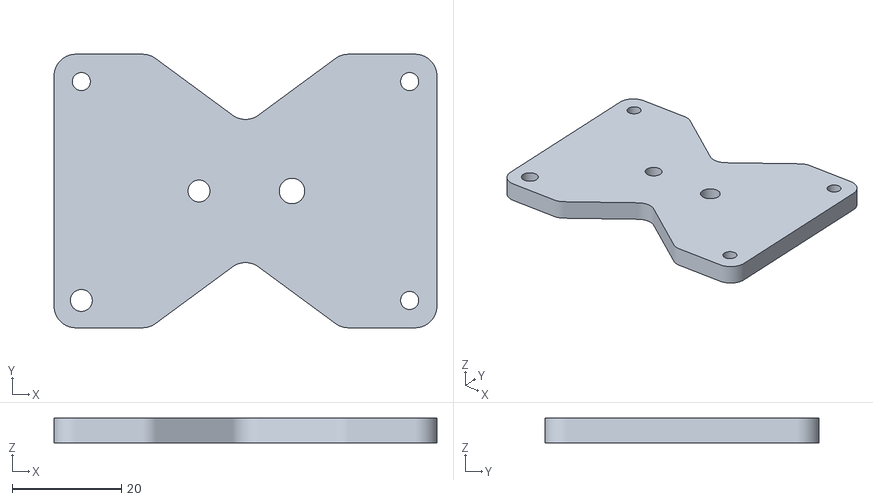
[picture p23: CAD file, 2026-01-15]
display/Billig-HMI Display case remix-Adapter plate-.stl
70.0 x 50.0 x 4.50

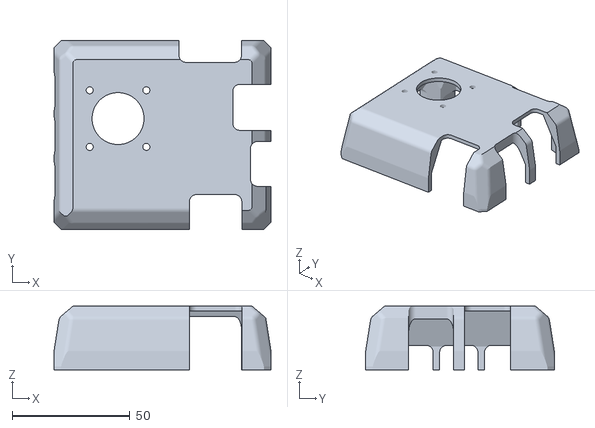
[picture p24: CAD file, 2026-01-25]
pcb/case/case_top.stl
92.0 x 80.0 x 27.0

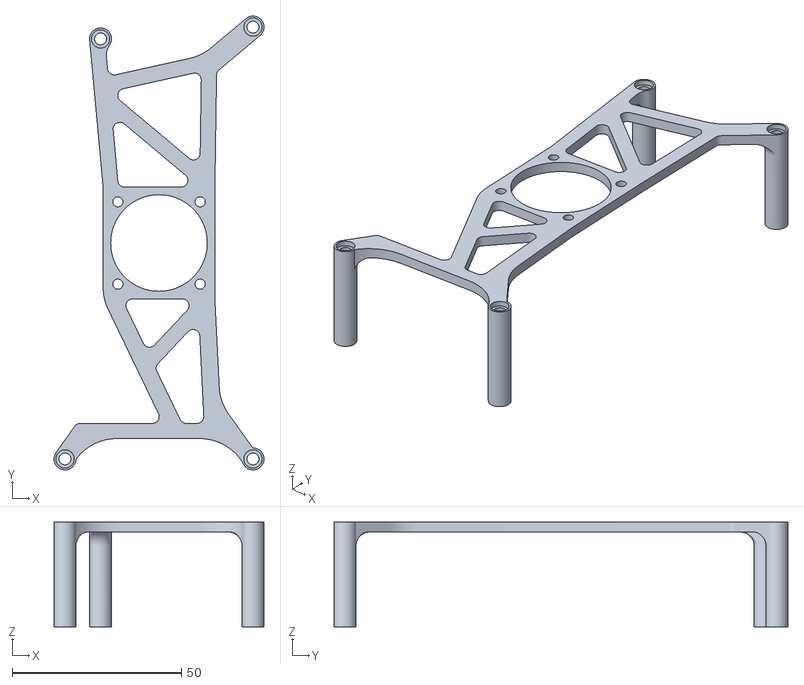
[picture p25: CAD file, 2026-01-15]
printer/stls/DIN/Billig-DIN mounts-MB-Top-.stl
62.0 x 134.0 x 31.0

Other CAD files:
printer/stls/Electronics mount/Billig-Electronics housing-top_cover_right-.stl
printer/stls/Endstops/Billig-Gantry-Endstop-Fix-Y-2-18mm.stl
printer/stls/Extras/kabel-clips_oval_v3.stl
printer/stls/Fixes/Billig-Toolhead-Backplate-.stl
display/Billig-HMI Display case remix-HMI_CASE_BOTTOM-.stl
display/Billig-HMI Display case remix-HMI_CASE_TOP-.stl
display/HMI_CASE_TOP.stl
printer/stls/DIN/Billig-DIN mounts-MB-Bottom-.stl
printer/stls/DIN/DIN-mounts-Step-Down.stl
printer/stls/DIN/din-clip-redux-heatset-4.2mm.3mf
printer/stls/DIN/din-clip-redux-heatset-4.stl
printer/stls/DIN/pcb_din_clip_x3.stl
printer/stls/Electronics mount/Billig-Electronics housing-top_cover_left-.stl
printer/stls/Endstops/Billig-Gantry-Part-X-V1-.stl
printer/stls/Extras/4x-Z-Leadscrew-Spacer.stl
printer/stls/Extras/Billig-Random small stuff-CableExtender Top-.stl
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

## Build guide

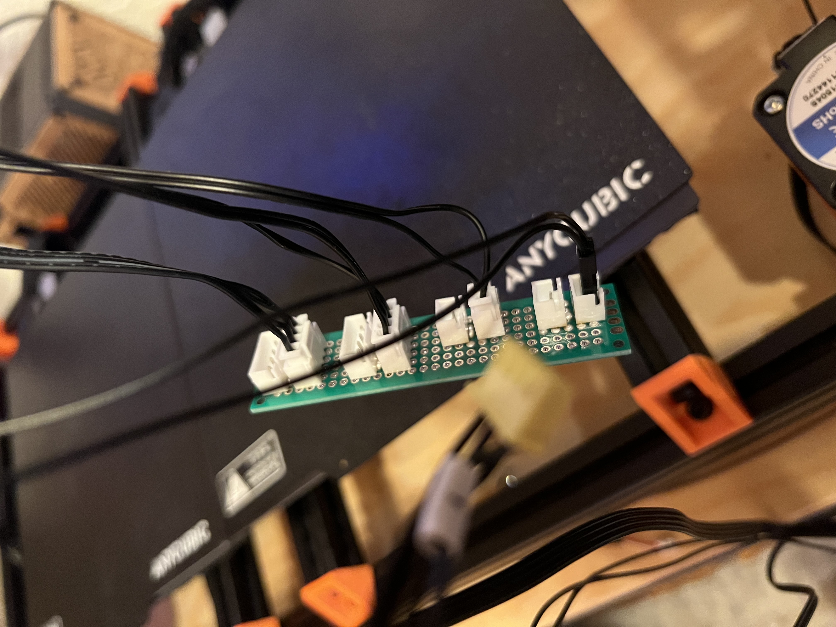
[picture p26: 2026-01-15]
assets/building/IMG_4192.jpg

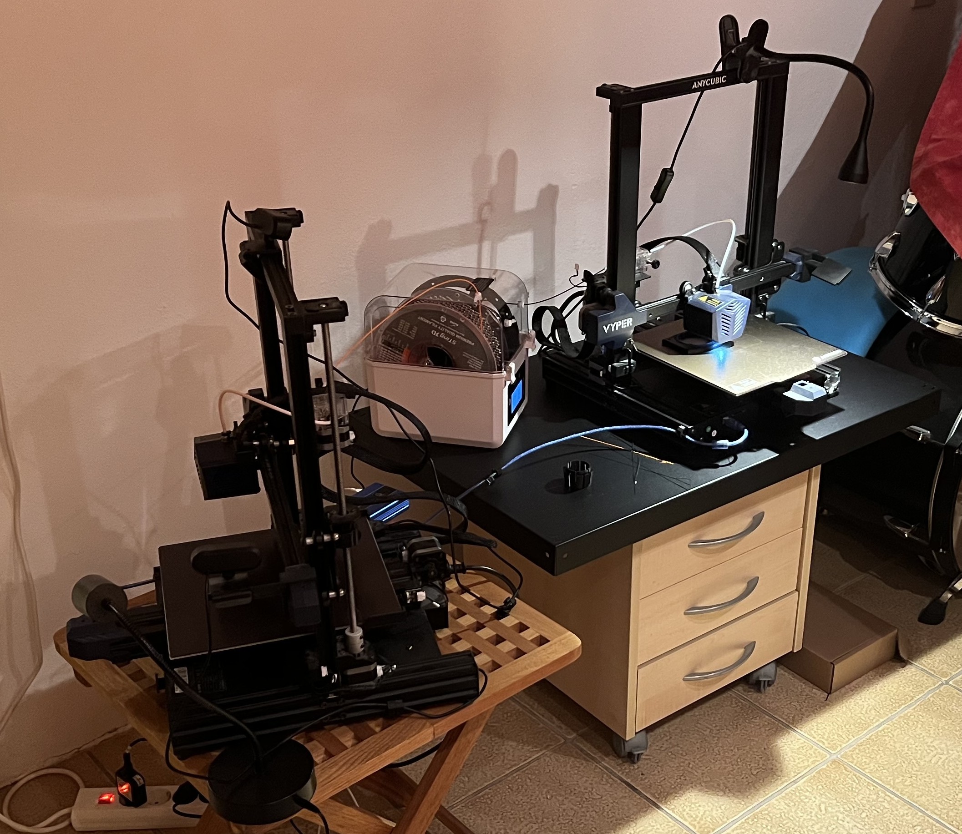
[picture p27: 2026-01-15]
assets/building/IMG_1979.jpg

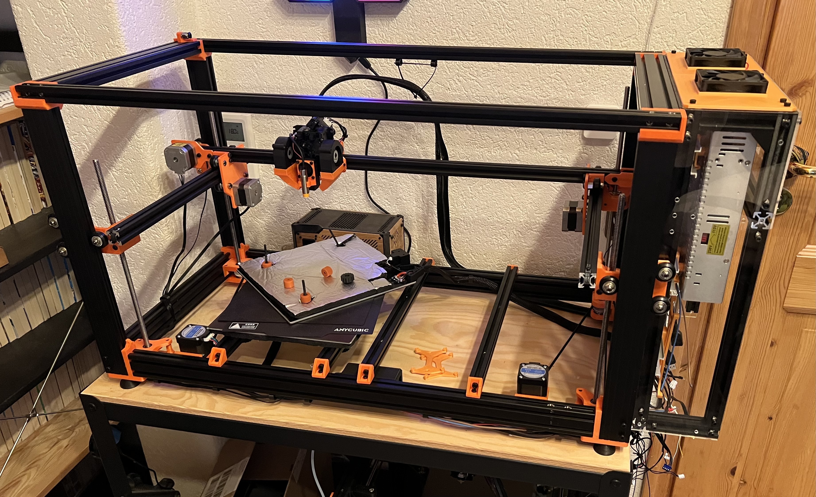
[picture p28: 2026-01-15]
assets/building/IMG_4209.jpg

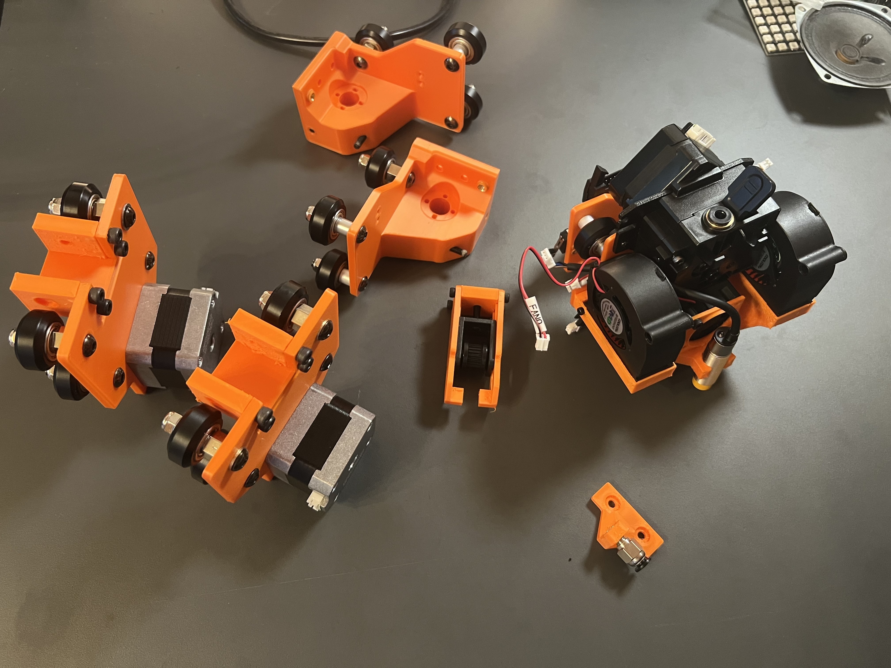
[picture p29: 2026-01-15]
assets/building/IMG_1974.jpg

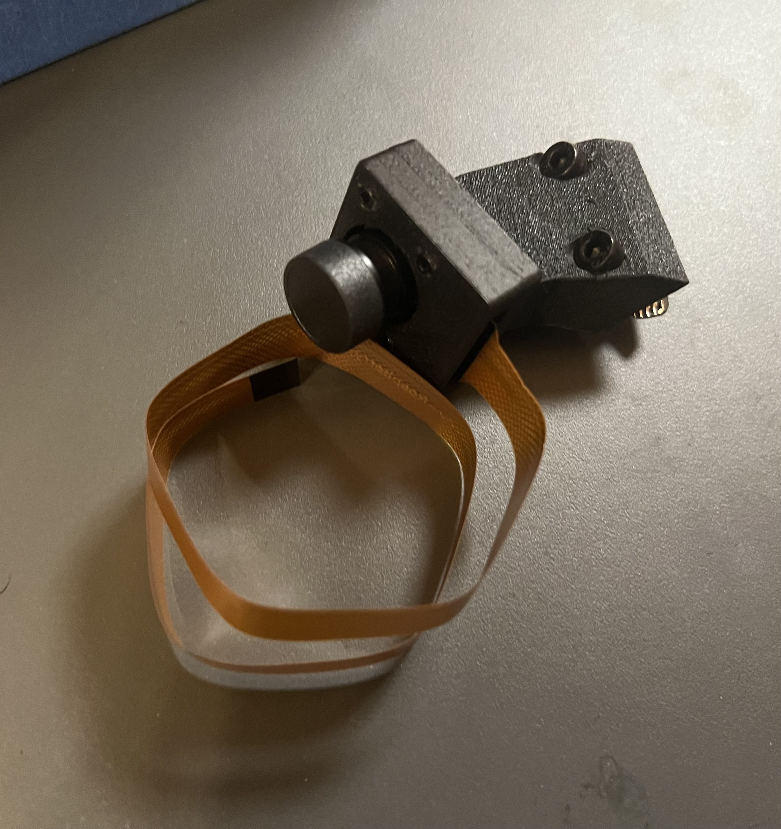
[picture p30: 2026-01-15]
assets/building/IMG_1973.jpg

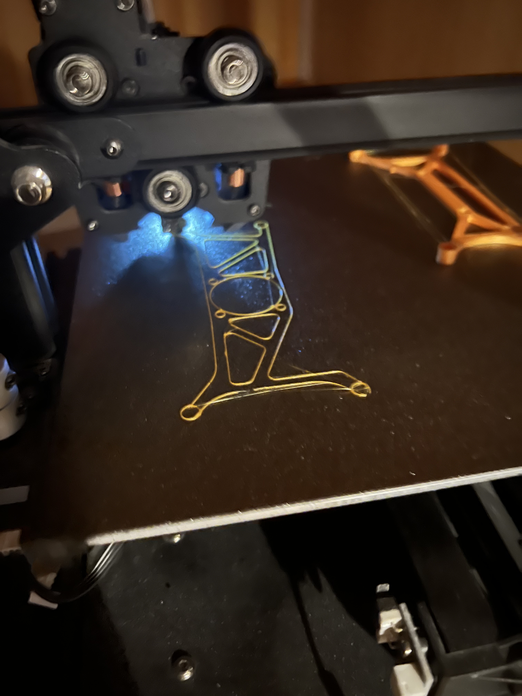
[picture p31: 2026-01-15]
assets/building/IMG_2151.jpg

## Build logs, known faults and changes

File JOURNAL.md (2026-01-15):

**Done:** **YES!! [Click here to see it's first benchy!](#july-13th)**  
**Result:** *~500$ 440x230x260mm 3D printer*

**Author:** [@playlogo](https://github.com/playlogo)  
**Repository:** [https://github.com/playlogo/billig](https://github.com/playlogo/billig)  
**Total hours so far:** - *lost count*  

**Bom**: [Google sheets](https://docs.google.com/spreadsheets/d/1451xPwitG2cd0BywjLuyT1Flae_F1tCVU7JKSqZtRoc/edit?usp=sharing)  
**CAD**: [Onshape](https://cad.onshape.com/documents/d0a1f0aa5ccbfda89a60ed00/w/724bd13dc87be16ac72aafeb/e/c63896b50a2324a549602fe6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)

About the printer:

- 440x230x200mm printing volume
- 940x410x465mm frame
- Reuses a lot of parts from two "broken" [Anycubic Kobra 2 Neos](https://de.anycubic.com/products/kobra-2-neo)
- Direct drive extruder & dual 5020 part cooling
- Completely enclosed electronics
- Build-in ABL
- With a rpi zero & Klipper-Ready
- ~$500 (including the two broken printers)
  
## Phase 3: Building

### July 16th

Create a NeRF and a super fancy marketing video for it :D

Flyby

### July 14th-15th

Improved the config, added Z-tilt adjust, pressure advance, leveled the bed (it was kinda lopsided) and probed (many) bed-mesh(s).

Here's my favorite one: Over 1.5mm difference from one side to the other

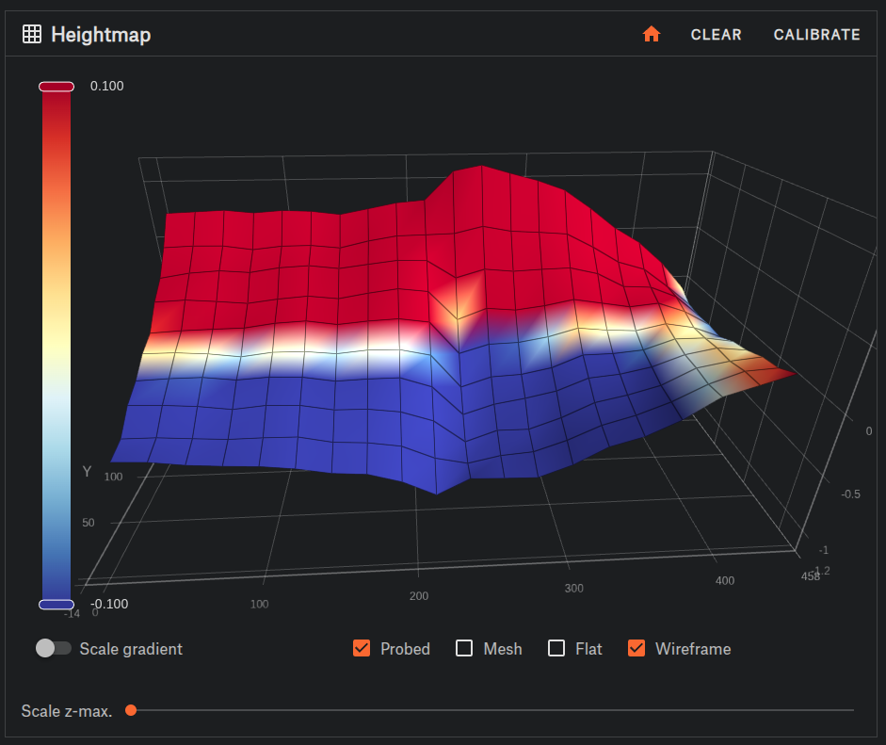
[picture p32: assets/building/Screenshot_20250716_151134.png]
Hilside


(Also I really really like the build-in [~~Prusa~~Billig-Research theme in Mainsail!](https://docs.mainsail.xyz/overview/features/built-in-themes)!)

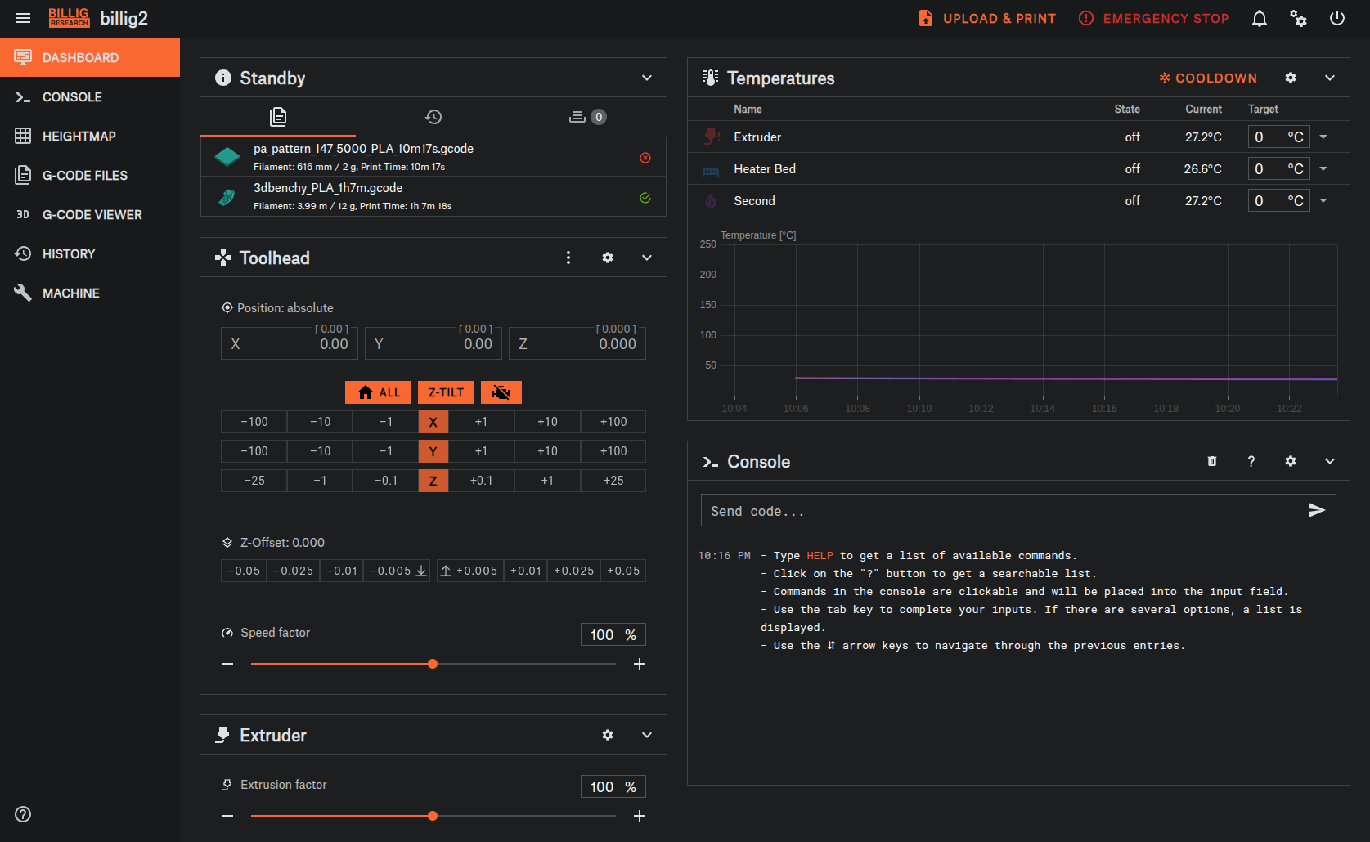
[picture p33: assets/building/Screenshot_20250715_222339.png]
Mainsail


### July 13th

More klipper configuration and wiring fixes.

Toward the evening (or midnight, depending on how you define that) I got it to print it's first bench!

Benchy!

I'm super proud of it, just look at it. No layer shifting (only minor extrusion issues and some stringing since the filament is super old)!!!

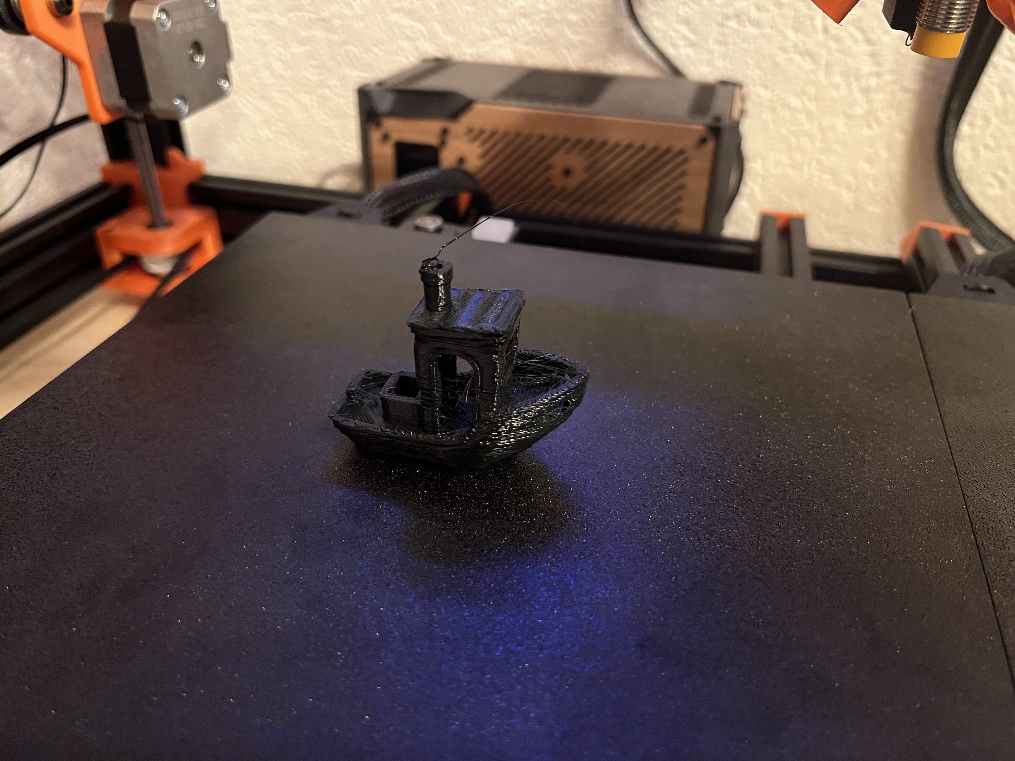
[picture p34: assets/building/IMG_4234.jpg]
BNenchy again


And the electronics look so cool!

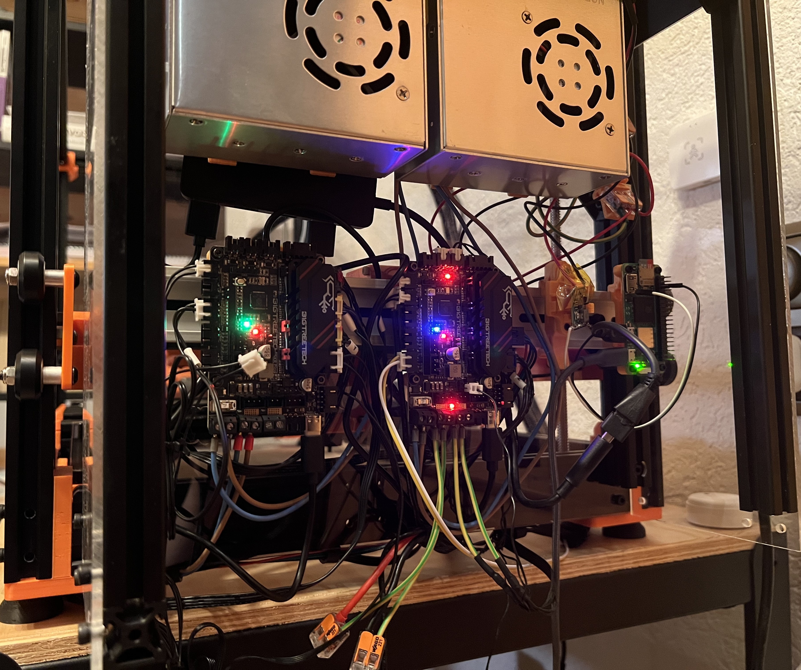
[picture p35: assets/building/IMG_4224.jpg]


While trying to debug the Z-probe I manged to release the magic smoke of one of the toolhead breakout boards I reused from the defective printers.

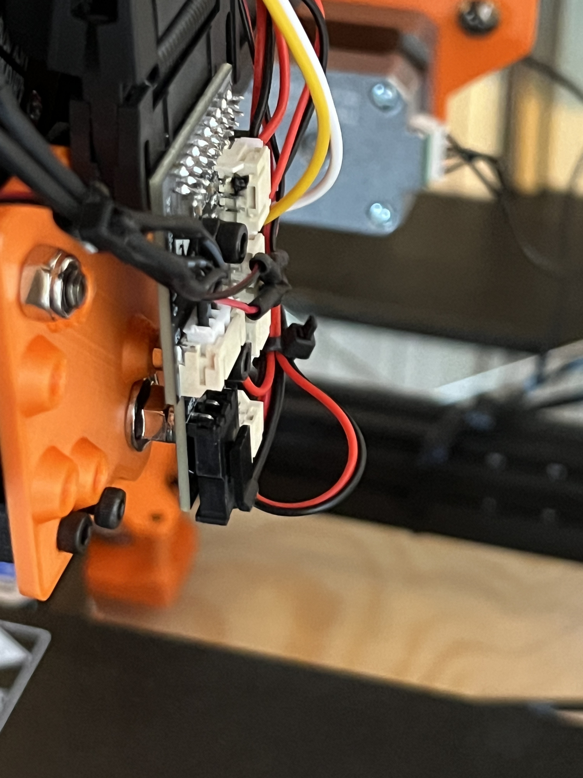
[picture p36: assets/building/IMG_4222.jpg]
Smoke


### July 12th

Wired up the new SKR picos, flashed klipper (took a whooping 5min...) and started configuring klipper to get the printer to home. (Only on the X&Y axis though).

At this point I was still using physical switches as endstops for the Y-Axis, later I switched to sensorless homing (thanks to the TMC2209!), since that made aligning the two Y-Motors way easier.

Also the case for the touchscreen finished printing and got mounted!

homeing

### July 11th

A new SKR pico arrived! Also the touch screen from elecrow arrived and I designed a case for it! (And got sidetracked by another project)

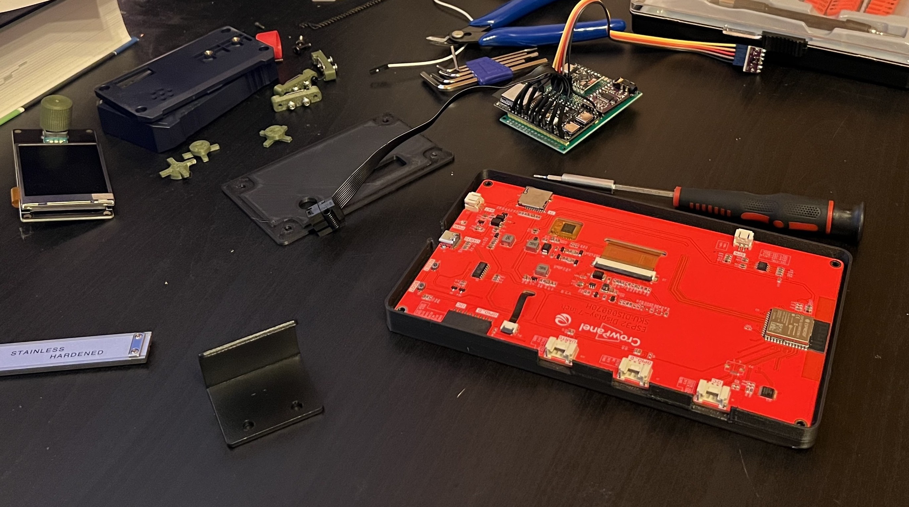
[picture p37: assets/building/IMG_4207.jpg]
Screen


### July 10th

The SKR picos arrived! And one was used....... **** you Amazon.

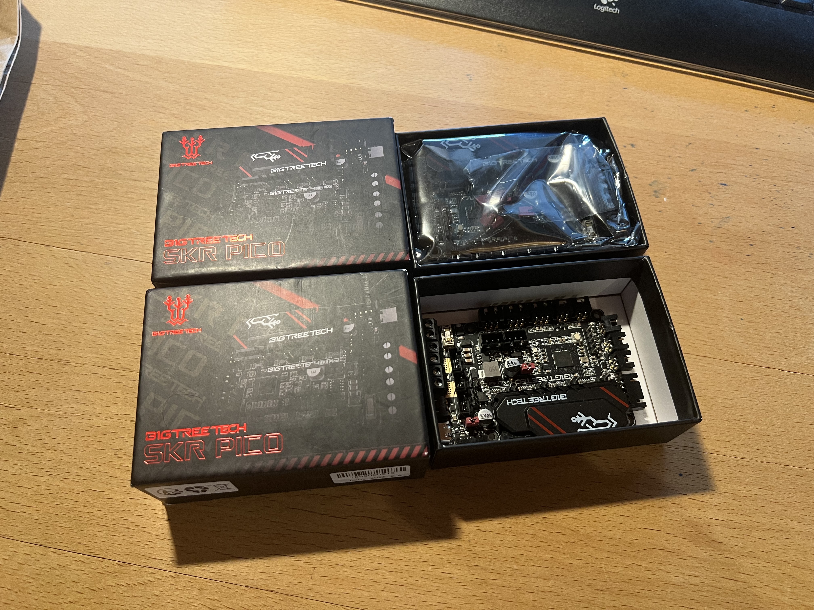
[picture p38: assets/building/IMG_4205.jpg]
SKr picos


### July 9th

After wasting even more time with SWD I just bought (and overpaid for) two BTT SKR picos on amazon with next day delivery.
(I also bough a proper [clone] ST-Link debugging adapter from aliexpress that will arrive at *sometime*)

### July 8th

Desperately tired to install klipper on the two TriGorilla V_4.0.1 (the control boards from the defective printers)... Turns out this specific board uses the `GD32f303RGT6` mcu with a broken bootloader - so you cannot flash it. I tried tons of different SD cards, different klipper build targets, and flashing them via SWD using a debugprobe (a rpi pico running some [firmware](https://github.com/raspberrypi/debugprobe)) using openocd. I once managed to "successfully" flash the original manufacture firmware back onto it:

```text
sudo openocd -f flash_config.cfg -c "program origina  
l.bin 0x08000000 verify reset exit"  
Open On-Chip Debugger 0.12.0  
Licensed under GNU GPL v2  
For bug reports, read  
[...]
xPSR: 0x01000000 pc: 0xfffffffe msp: 0xfffffffc  
** Programming Started **  
Info : device id = 0x21040430  
Warn : STM32 flash size failed, probe inaccurate - assuming 1024k flash  
Info : flash size = 512 KiB  
Warn : Adding extra erase range, 0x0805b534 .. 0x0805b7ff  
** Programming Finished **  
** Verify Started **  
** Verified OK **  
** Resetting Target **  
shutdown command invoked
```

But it didn't turn on anymore... For some reason some person decided that disabling the SWD-reset wire in the rp2040 version of the debugprobe firmware would be a good idea, so if you need that (which you do!), delete the `#if false` and `#endif` line in [this file](https://github.com/raspberrypi/debugprobe/blob/466432c5eb8d3c4a70842833804996c15ed18c51/include/board_pico_config.h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) and recompile it!
I also had a extremely hard time connecting to the chip via SWD, since the reset (with the lines remove) still only worked in about ~10% of the tries...

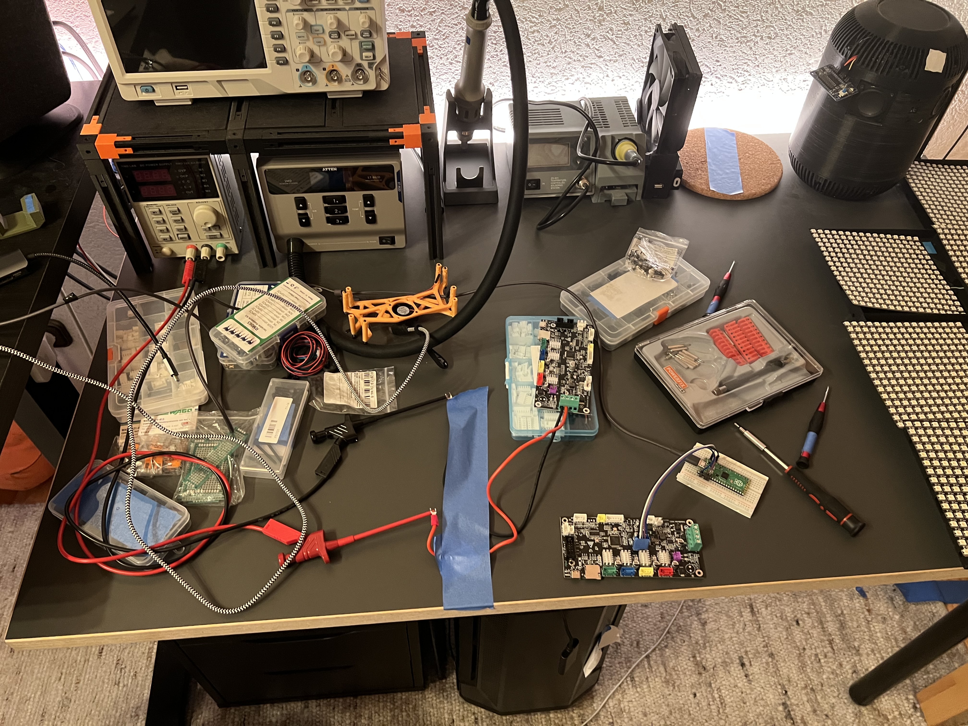
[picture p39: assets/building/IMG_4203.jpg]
Picoborbe


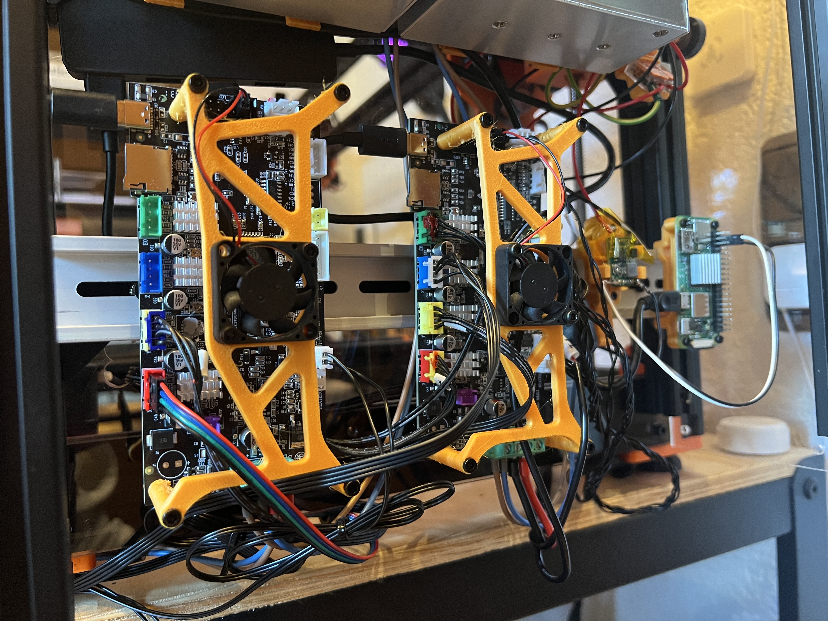
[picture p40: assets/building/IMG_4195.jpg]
MCUs


### July 7th

Designed & build a little wire extending box for the steppers on the left side & chaotic wiring.

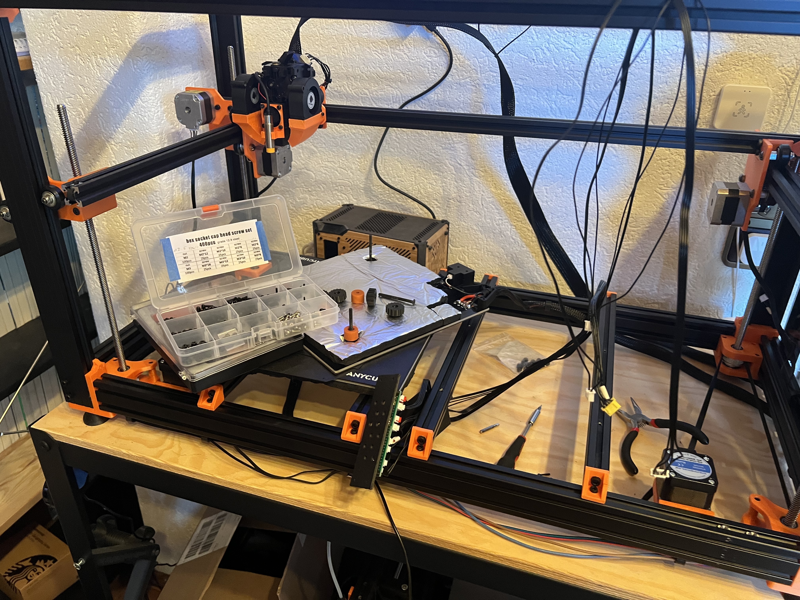
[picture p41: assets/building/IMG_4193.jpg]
Extender


### July 1st

Added fans for electronics section, started wiring for Y-Gantry & Z-Motors.

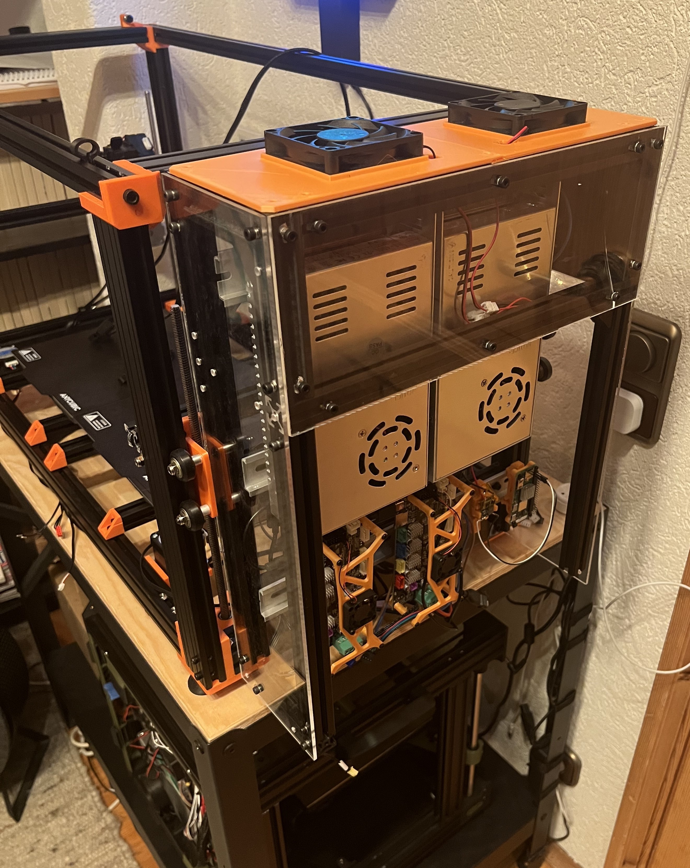
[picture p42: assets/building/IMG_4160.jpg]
onlyfans


### June 26th

Back from holiday!

Did the Mains & 24V wiring (which didn't blow up!) using a old power cord that now doesn't exist anymore.

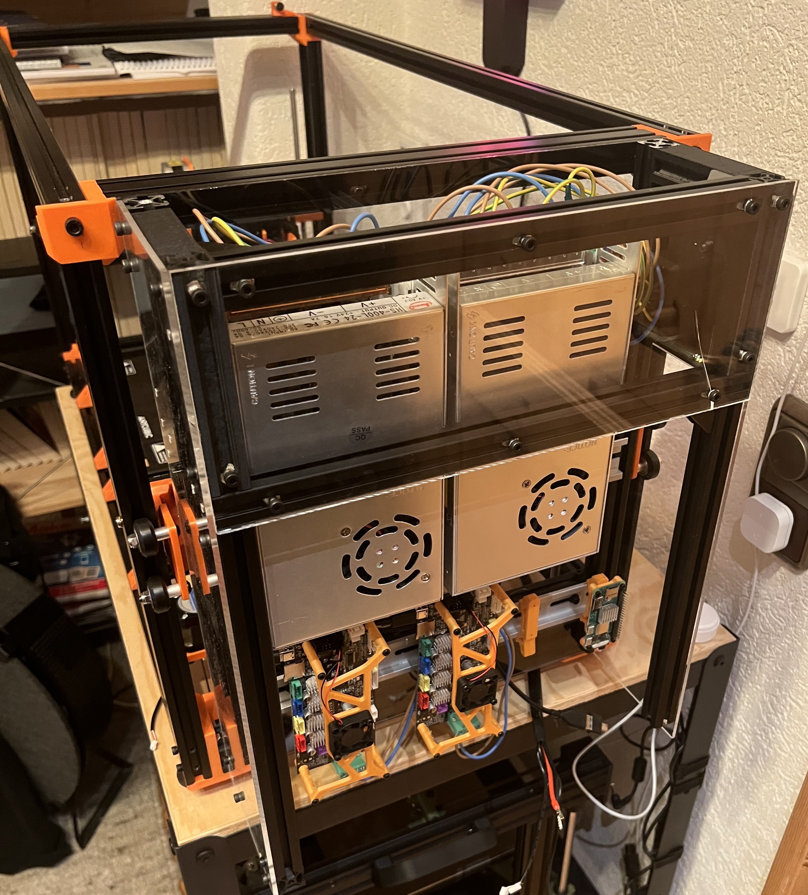
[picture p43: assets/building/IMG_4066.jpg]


### June 1st-10th

Still in the final exam phase, so not that much progress, BUT:
I mounted the PSUs (yep, 2), the original control boards (from the 2 broken printers) and other stuff including the electronics enclosure.

(Made no picture of them, see next entry)
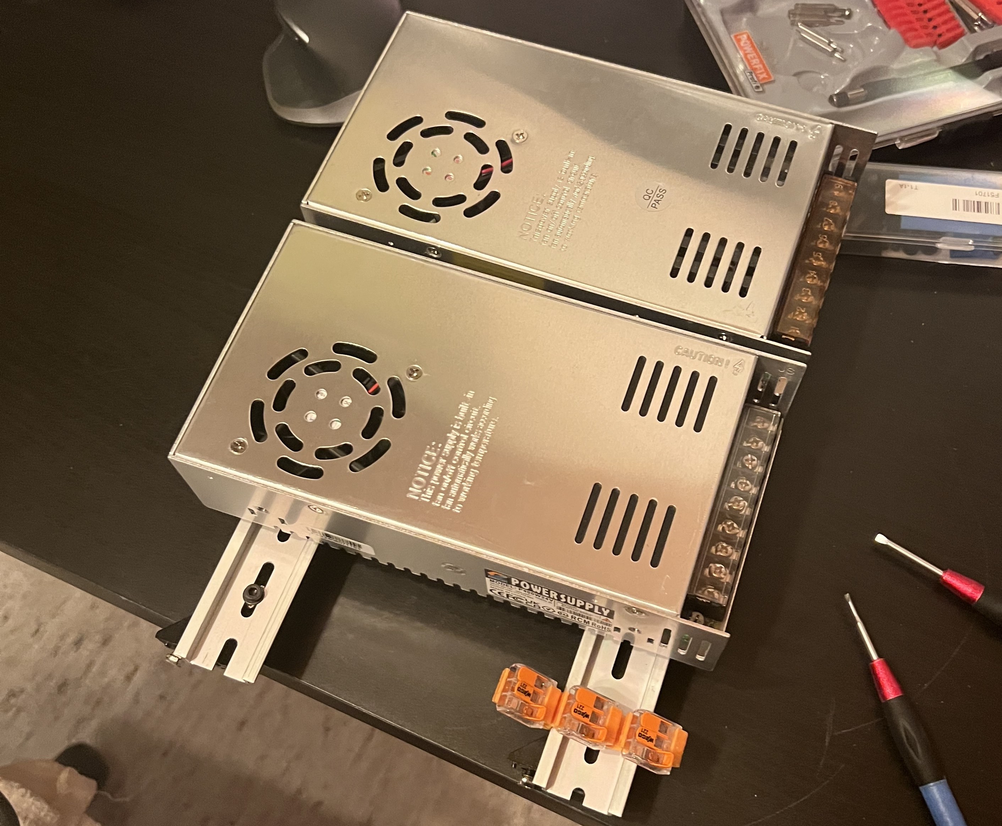
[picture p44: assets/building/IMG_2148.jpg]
PSU


### May 21th

Insulated & mounted the beds & assembled and installed the XY-Gantry (using the subassemblies from before).

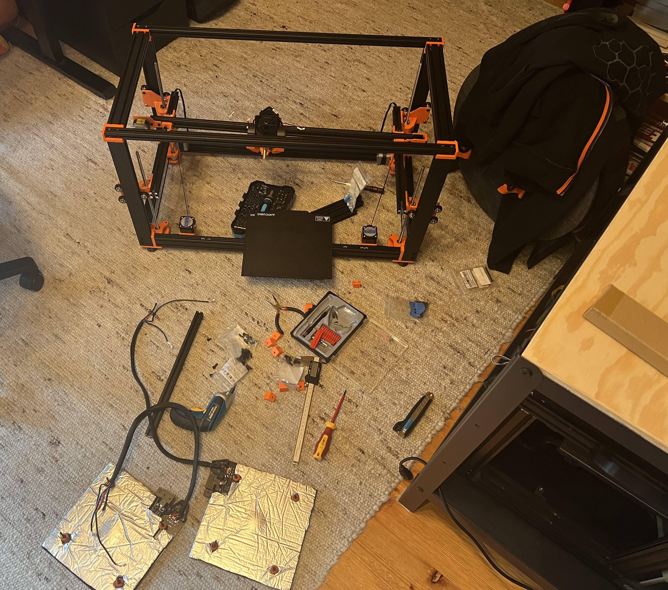
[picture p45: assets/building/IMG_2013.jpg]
Insulated beds


I'm really happy with how the design turned out!

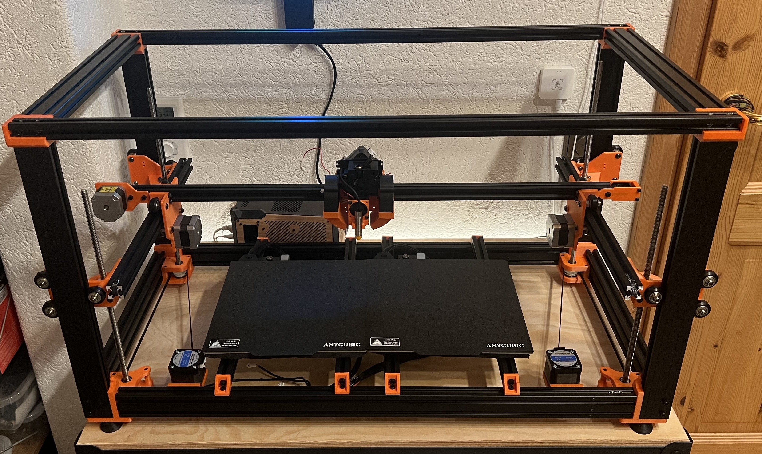
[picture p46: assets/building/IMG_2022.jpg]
the printer


### May 20th

Assembled the top part of the frame - Not much more to say, apart from that my taps weren't perfect (which meant that I couldn't use all screwholes, but who cares... It will be strong enough anyway right... right ?)

Top part of the frame

### May 19th

Assembled the bottom part of the frame!
With enough force every fitted together nicely and it's also somewhat square, i'd call that good enough.

Foreshadowing: The leadscrew in the top left (which was a spare I had lying around) has the wrong pitch...

Bottom part of frame

### May 15th

Assembling the new drill press, and drilling all the left over holes in 1h... I hate that cnc

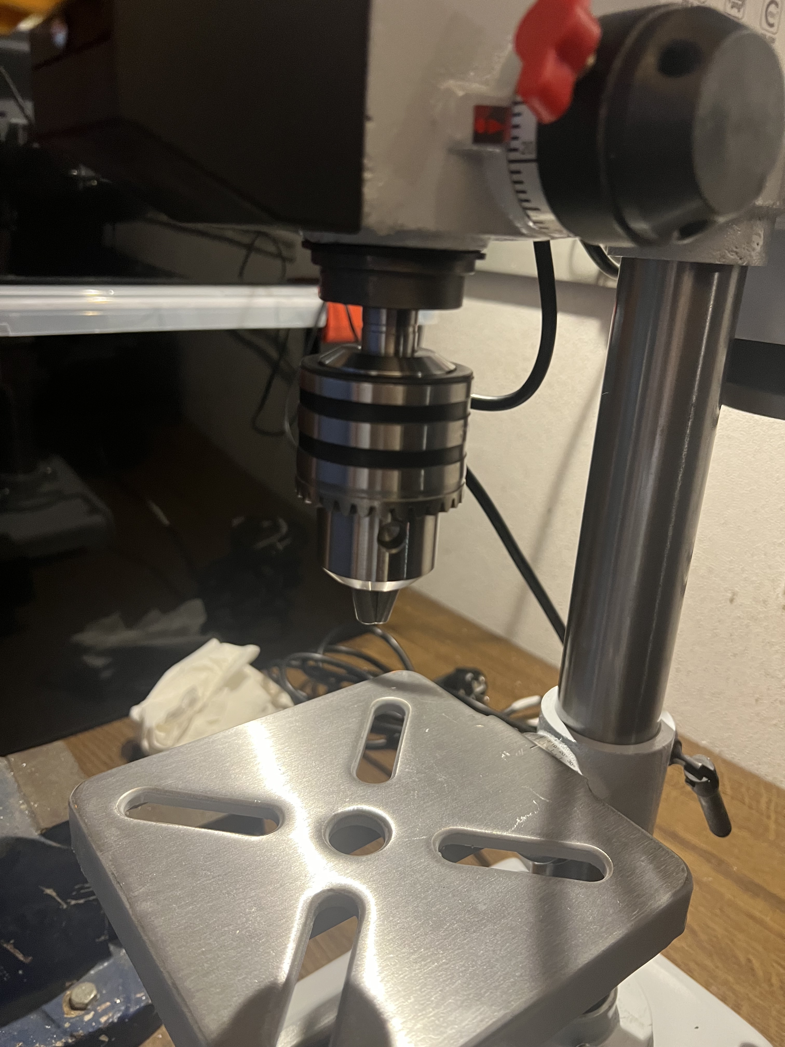
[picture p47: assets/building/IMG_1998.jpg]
Drill press


### May 14th

I'm so done with aluminum profiles, I should have just payed ~$50 more to have them to the drilling and tapping.

### May 13th

Tapping & Drilling - Fun...

To save money I decided to tap all aluminum proifles and drill all necessary blind holes in them myself. There were a lot of taps and holes - and I though that using a (already heavily modded!) 3018 CNC for drilling the holes would be a good option...

Drilling holes using a 3018cnc

It worked (i'll give it that much), but it took around 10min per hole with a feed rate of a staggering 2mm/min... Cannot recommend

Tapping the ends of the extrutions turned out to be a rabit hole too: [this is not made up!]

- After tapping ~10 holes the $1.80 tapping tool from aliexpress got dull... -> Ordered new ones form aliexpress
- Same day, since I didn't want to pause for a week until they arrive: Buying a new tap from the local hardware store only for it to snap in half after 3 holes (to be precise, IN the 3rd hole, it's still in there)
- Still same day: Getting a new tap from the local hardware store only for it to snap in half after 2 holes (to be precise, IN the 2nd hole, it's still in there) - yes
- Still still same day: Getting a new tap from the local hardware store (my third time today being there) only for me to be too scared to use it
- Still same day, same hardware store visit as above (at ~19:40): Impulse buying the cheapest drill press since I don't want to use that cnc anymore

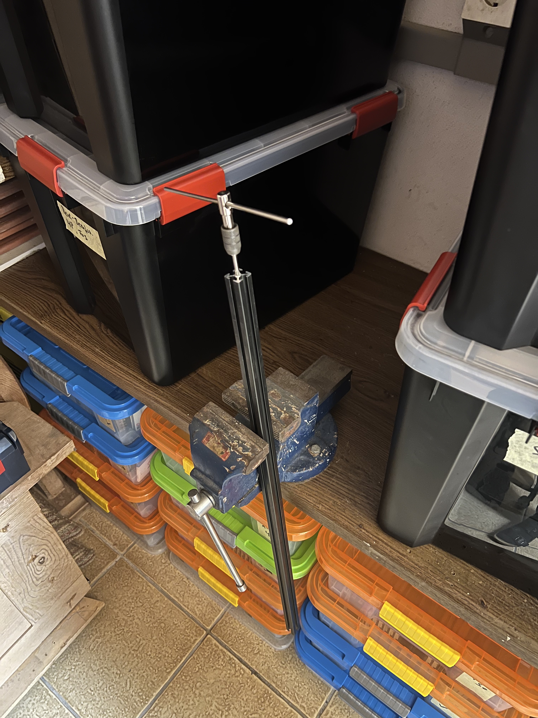
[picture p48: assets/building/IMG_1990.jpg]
Tapping


### May 11th

Assembled all smaller subassemblies + the camera mod for the Ender3NG, lot's of heat-set inserts (Hackadot leak)

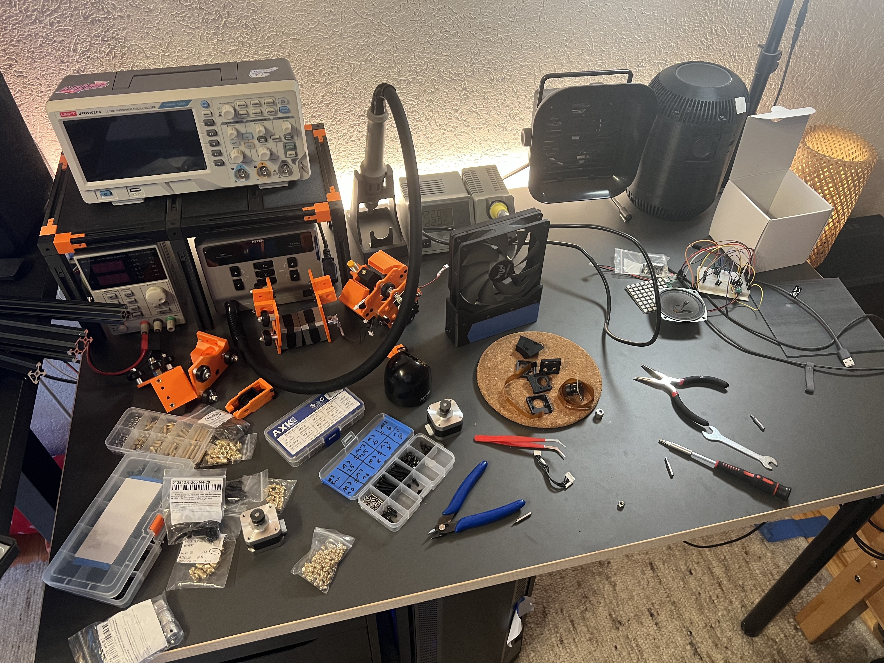
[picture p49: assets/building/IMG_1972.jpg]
Assembly of subassemblies


### May 4th

More printing over the last few days, most parts have now arrived - So far everything seems to fit together

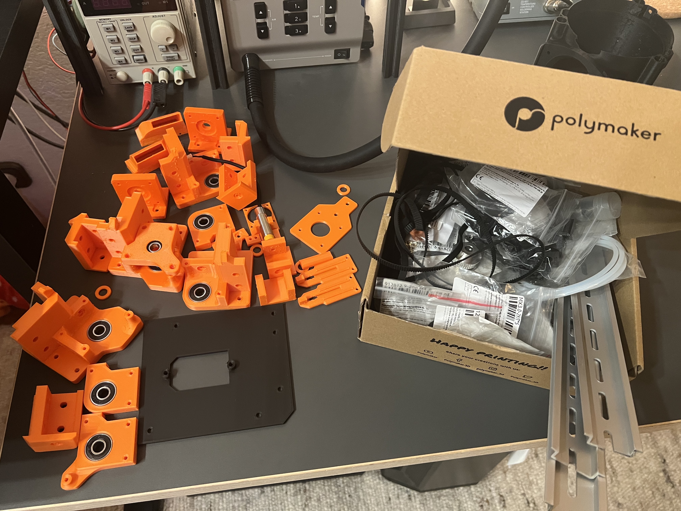
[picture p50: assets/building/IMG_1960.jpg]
Progress parts


### Rest of April

Not much progress here, due to final High school exams - Started printing parts towards the end of April, and rage bought the cheapest 2 role filament dryer (Sovol SH01) since the parts looked like this:

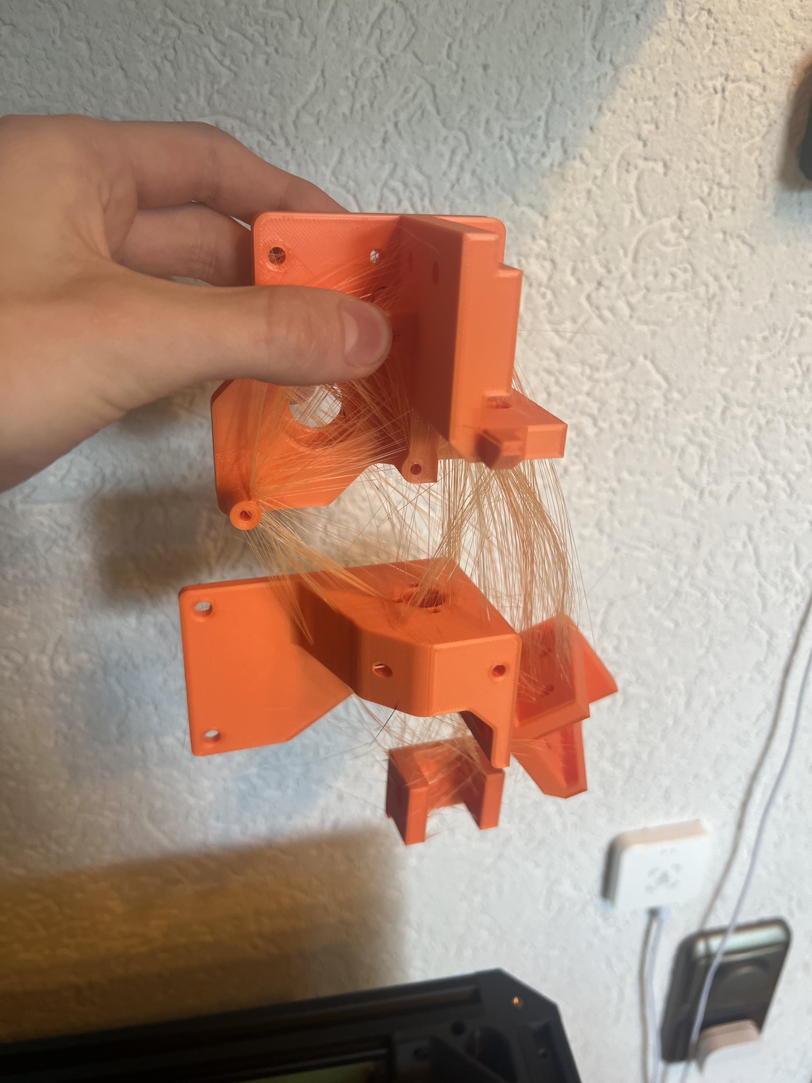
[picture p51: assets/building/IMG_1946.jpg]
Stringing


## Phase 2: Design

[Written on April 7]

> Take a look at the [Design-Notes](https://github.com/playlogo/billig/blob/main/notes.md) to better understand my design decisions!

> Take a look at the [PCB](https://github.com/playlogo/billig/tree/main/pcb/readme.md)!

[Written on April 7]  
About this part of the journal: So journaling didn't really work out that well. I started planning the printer and a timeline ~4 weeks ago on March 9., but then got sidetracked by other things (hackboard, pre-final school exams, irl stuff). During this time I constantly thought about it though, and decided to try to convert 2 broken [Anycubic Kobra 2 Neos](https://de.anycubic.com/products/kobra-2-neo) into *this* one big printer, instead of buying all parts brand new.

After all, this project was a lot of fun and very interesting. Once I got into the "CAD design mood" I really enjoyed doing it, and I've also learned **a lot** about Onshape and how to approach big projects and design parts, that are internally dependant on each other. I'm proud of the final design :)

### April 8th - Tuesday (1 day after deadline)

Small improvements & fixes: Improved 'Design notes', fixed spelling mistakes, added JST cables to BOM, added PCB mount to CAD model

### April 7th - Monday (today)

*I really want a break from cad plsss!*

Today I fixed a lot of small stuff in the CAD model: I added endstops for X&Y, a X-Motor mount, X-Belt tensioner, changed Y-Motor position from *fixed at one end of the extrusion* to *on the X-Plate*, improved dummy models of steppers/lead screws/etc, fixed a lot of small bugs in the CAD model, created the PTFE tube holder and created the electronic housing.

The electronics housing safely mounts both PSU, control boards, rpi zero and power plug. It's surrounded by acrylic panels, and has two fans at the top to suck in air from the bottom though the entire assembly.

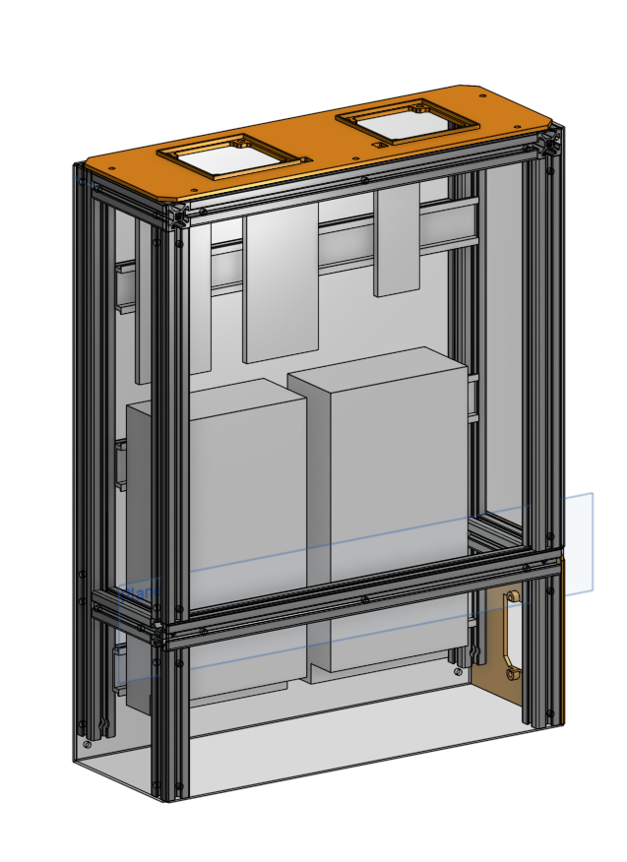
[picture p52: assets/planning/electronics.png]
Electronics


I also updated the BOM and created this document (and it's now past midnight).

Final version (V2.1 in CAD document history):
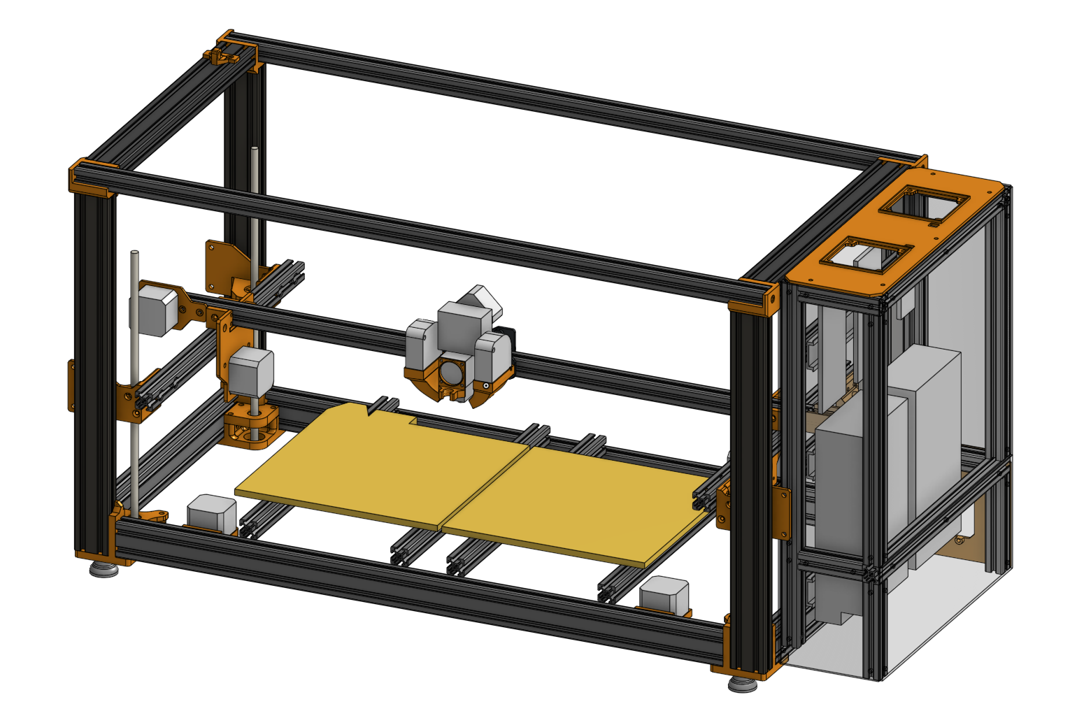
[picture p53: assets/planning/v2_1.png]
V2.1


**Time spend in CAD:** Last 7h (had to go to school until 13:10 to get grades of last 2 years and the admission notice for my final 5 tests)

### April 6th - Sunday

*Another caddy day (ahhhh)*

This day was super productive. I've designed the entire toolhead, reworked the entire gantry, and finally managed to create a **draggable 3 dimensional toolhead** in onshape, that allows me to test the reachable positions of the nozzle.

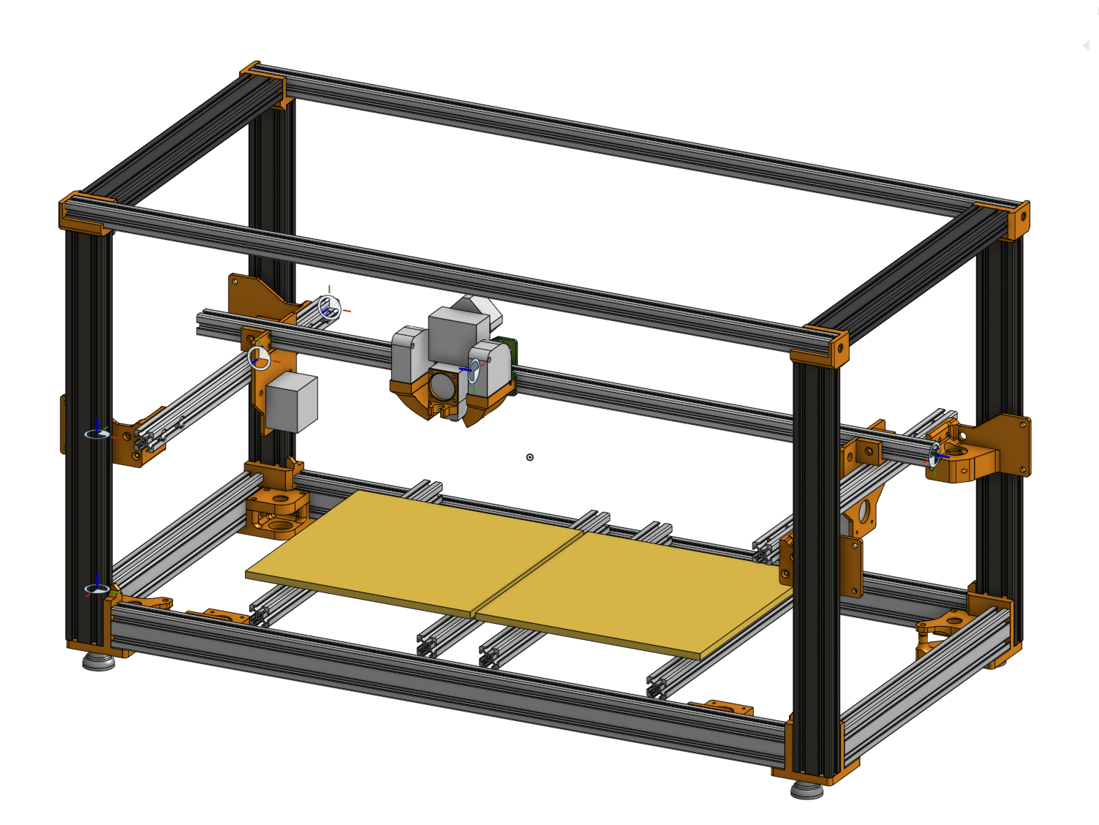
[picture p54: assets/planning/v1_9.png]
V1.9


Reworking the gantry was *a lot* of pain. This is my first time seriously using assemblies in Onshape, and I based the original gantry part assembly on a feature I deleted while reworking the frame (ahhh). This broke my entire gantry when I finally updated it's context, which I need to do, because I've extended it by ~8cm to allow the nozzle to reach all positions. This is a example of the pain I had to endure:

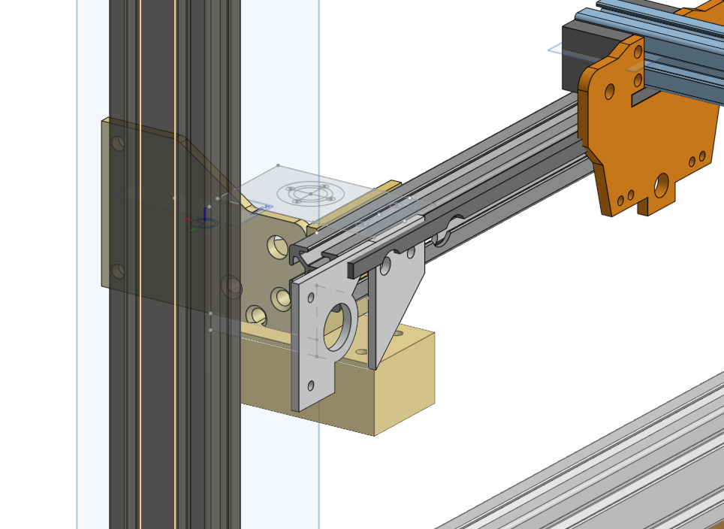
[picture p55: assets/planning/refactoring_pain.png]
Pain


**Time spend in CAD:** ~75% of my time awake (didn't even go outside) -> 10h

### April 5th - Saturday

*A caddy day*

On saturday I basically redid everything I did the day before. Instead of bolting the profiles strait to each other using blind joints, I took some inspiration of the Ender3NG, and created these "in-between structures" (see picture). I also converted this sketch (which I created the night before) into CAD (once again, inspired by the Ender3NG, but created from scratch and the final part also ended up completely different)!

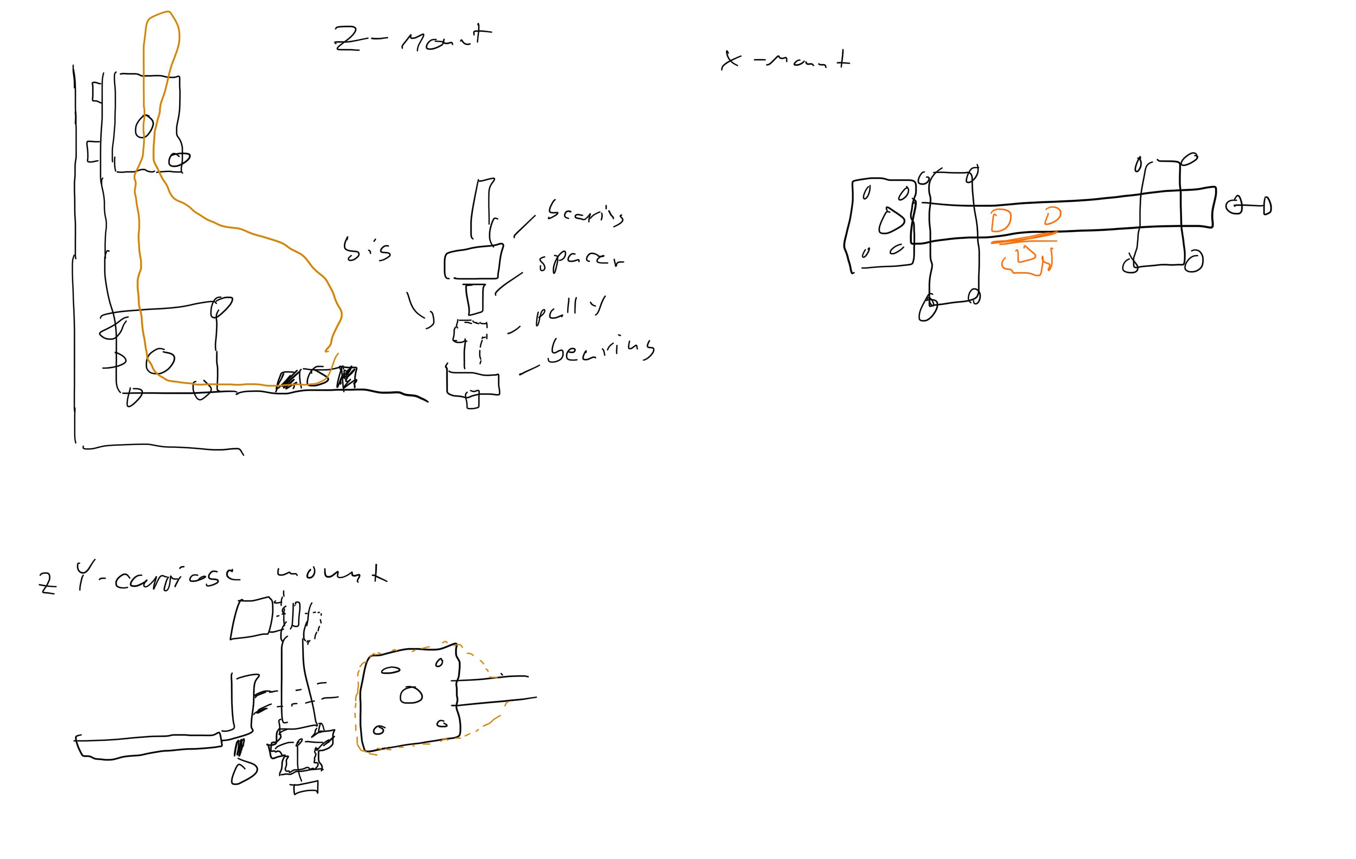
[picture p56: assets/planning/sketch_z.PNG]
Sketch of Z-Axis bottom mount

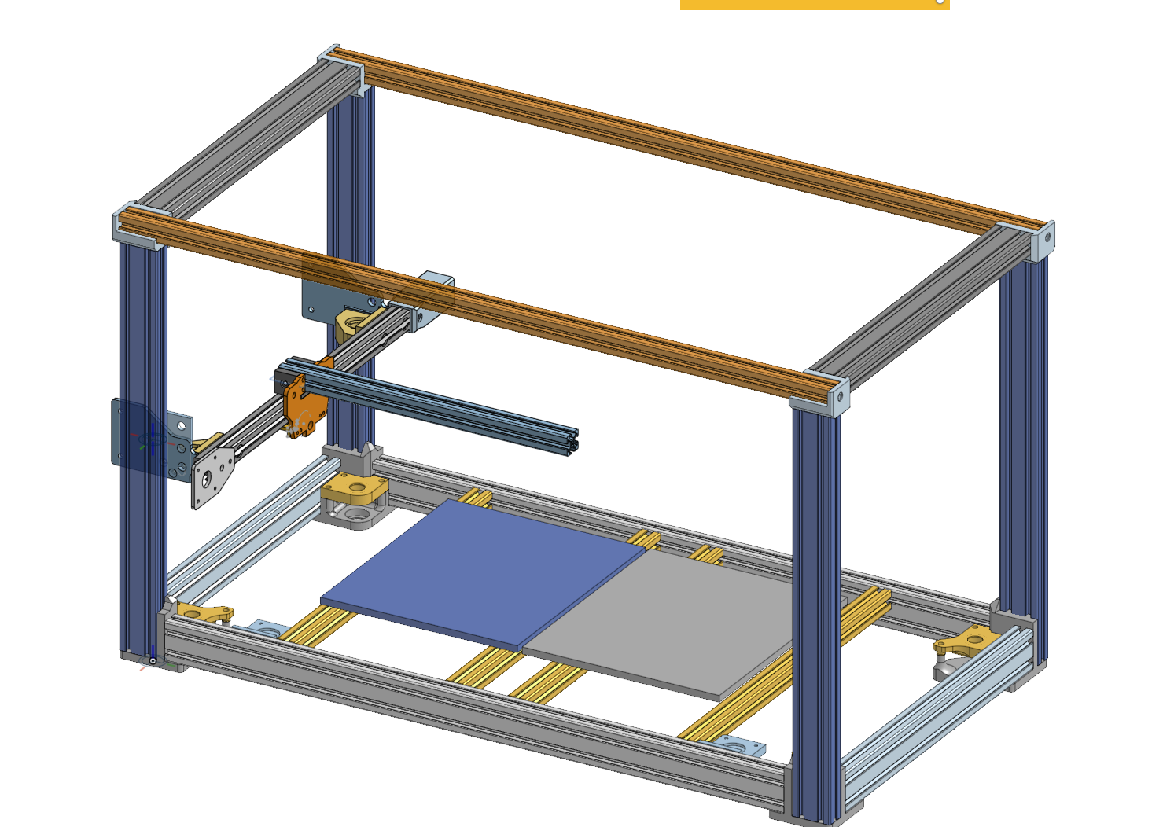
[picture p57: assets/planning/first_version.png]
Improved frame


I'm very happy with the progress one that day, cause the frame and gantry has been one of these low motivation, hard to imagine progress blockers. Also, the top "extrusion structure mounts" worked first time, and I never had to change them later

**Time spend in CAD:** ~60% of my time awake (pain, at least I managed to sit outside and enjoy the warm weather for 30min) -> 9-10h

### April 4th - Friday

4 Days ago I finally started to speedrun the entire CAD design starting with the frame (which I then redid one day later...). I started by converted these drawing I made about two weeks earlier during school into this frame:

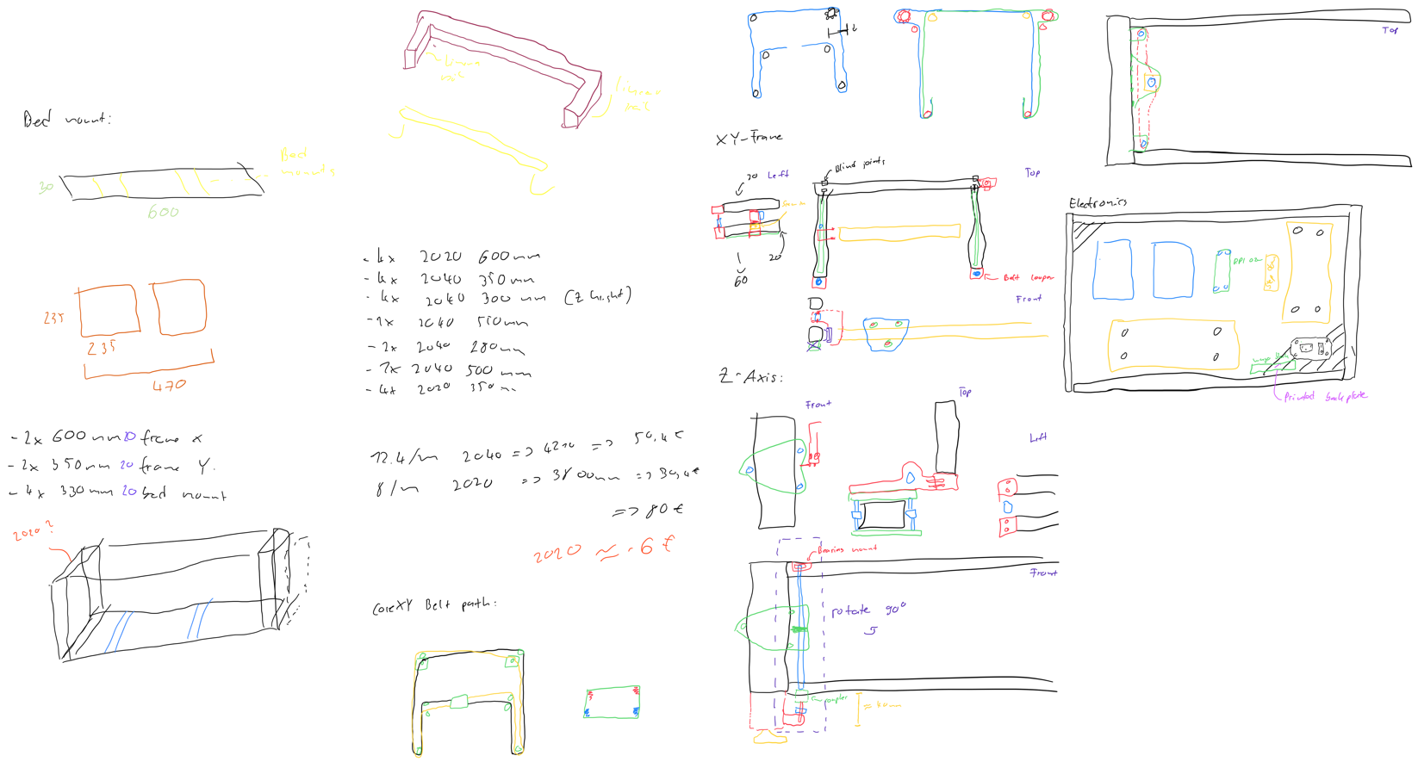
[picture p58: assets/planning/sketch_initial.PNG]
Intial sketches

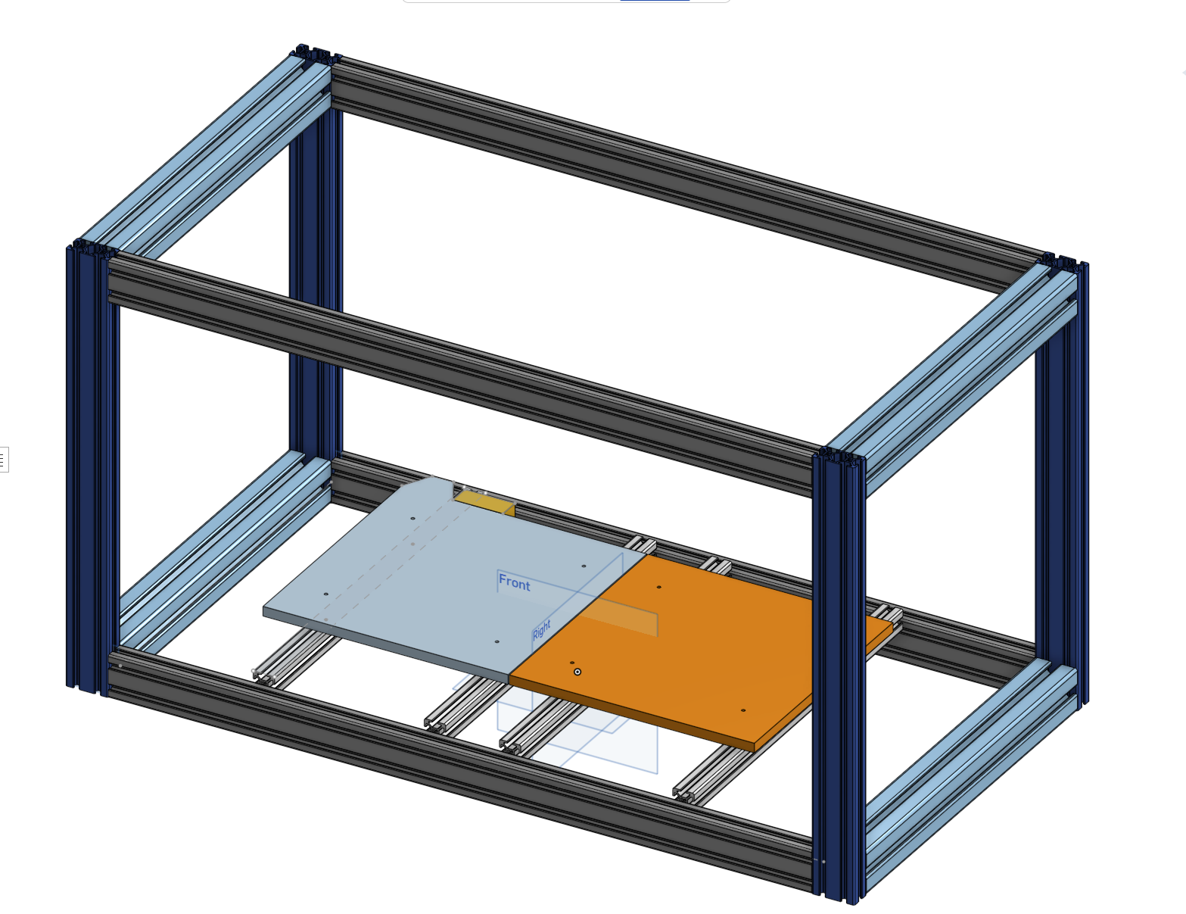
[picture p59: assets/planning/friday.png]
Initial frame


As you can see in the sketches, I was initially targeting a CoreXY build with linear rails, but this idea later got ditched in favor of a simple V-Wheel based Belted XY-Gantry to keep costs down.

I also started dissembling one of the broken printers to take measurements of the heatbed, etc.

**Time spend in CAD:** 2h during the morning (since I'm almost done with school, I don't have to go to every lesson anymore), 6h in the afternoon, evening and early night.

## Phase 1: Planning

**Note from July 17: This plan got totally ignored**

**Features:**

| Must-have | Should-have | Probably not enough time|
|---|---|---|
| (400mm)² for X&Y, Z should have 200mm+ | Filament runout sensor | 2 Build-in filament holders (Prusa Core style: inset into case, on the left&right) |
| CoreXY with Belts | LED-Bar under Bed for status, etc| Build-in filament weight sensor (using [one of these](https://de.aliexpress.com/item/33046037411.html))|
| Enclosed (for ABS) | Exhaust air filtration using [activated carbon](https://meltbro.de/nevermore-activated-carbon-aktivkohle-fuer-voron-2-4-0-1-0-2-trident-3d-drucker.html) | External [Multi-filament switcher (Pico-MMU, 2 filaments)](https://www.printables.com/model/1083174-mmu-multi-material-upgrade)|
| Direct drive | | |
| ABL using cheap [BLTouch clone](https://de.aliexpress.com/item/1005007554425544.html)| | |
| Temperature Sensor inside & Temp-control fans | | |

### March 8th - Saturday

Brainstorming about goal. Final 3 candidates:

- Print farm: Similar to [this](https://blog.prusa3d.com/wp-content/uploads/2021/10/DSC6780-scaled.jpeg) - Why not: Basically would only copy their design and scale it down, due to budget only 2 integrated printers -> kinda useless
- Module based: 250x250x100mm modules with only the heated, joinable in one direction, rack & pinion system on the sides, hotend on a ["crane" (picture explains it best)](https://image.made-in-china.com/203f0j00dwPqjhLbGOkI/Zpmc-Spreader-for-Rtg-Type-Container-Gantry-Crane.webp) - Why not: Budget would only allow ~2 modules -> Print volume way to small
- Billig (this): There seems to be no big (~(400mm)³) enclosed printer for under 1k -> Should be doable with only 300$ when cutting corners

Billig will be a mix of:

- [Prusa XL](https://blog.prusa3d.com/wp-content/uploads/2021/12/main_1.jpg) (frame design)
- [Voron 2.4](https://cdn03.plentymarkets.com/ioseuwg7moqp/item/images/29251/full/Copymaster3D-Voron2-V2-4-R2-SB-Kit-350-x-350-x-350mm-With-StealthBurner-29251.png) (artistic style)
- [Ender 3 NG](https://media.printables.com/media/prints/922401/images/7302744_6c89a110-ee20-4af6-ad0b-d029573e6b25_aa334db1-1287-41b3-9dea-289b26e3adf5/thumbs/inside/1280x960/jpg/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) (enclosure design)

Accepted tradeoffs:

- Longevity: Will be using the cheapest parts for everything
- Print speed: Won't be fast due to size
- Power draw: Will need A LOT of energy to heatup the entire chamber

Initial design ideas:

- Printbed consist of 4 [smaller (and cheaper) print beds](https://de.aliexpress.com/item/1005007288279620.html): ~ 40€ total

**Time:** 3h

*This was a triumph, Huge success*

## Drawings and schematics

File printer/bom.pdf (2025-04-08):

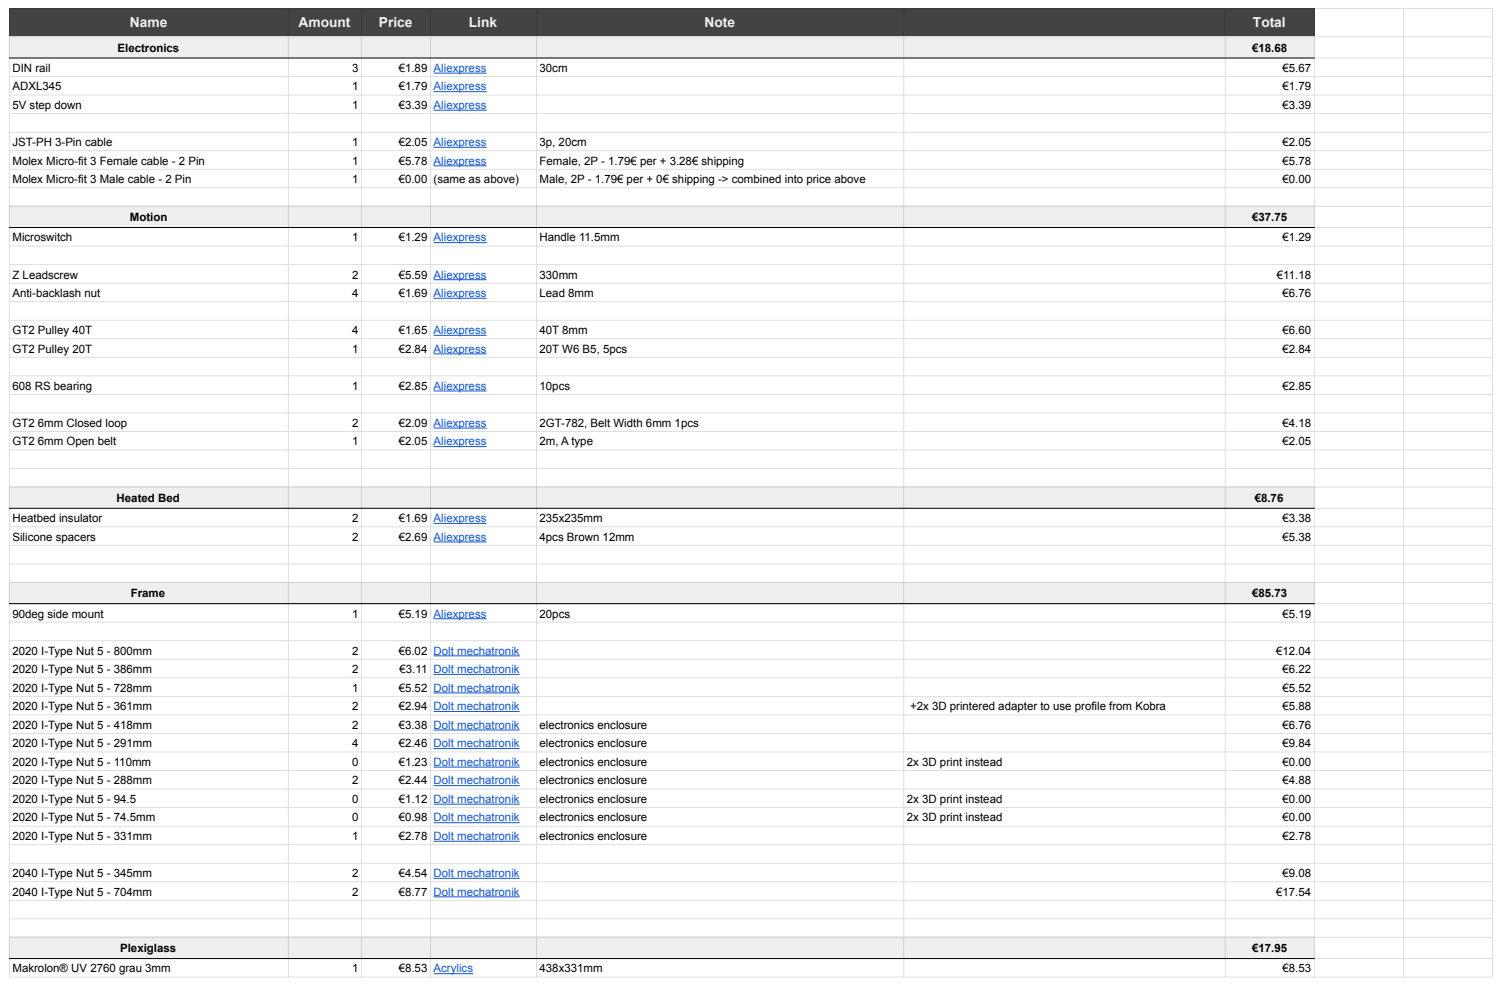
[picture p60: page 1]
DIN rail; €1.89 Aliexpress; ADXL345; €1.79 Aliexpress; 5V step down; €3.39 Aliexpress; JST-PH 3-Pin cable; €2.05 Aliexpress; Molex Micro-fit 3 Female cable - 2 Pin; €5.78 Aliexpress; Female, 2P - 1.79€ per + 3.28€ shipping; Molex Micro-fit 3 Male cable - 2 Pin; €0.00 (same as above); Male, 2P - 1.79€ per + 0€ shipping -> combined into price above; Motion; Microswitch; €1.29 Aliexpress; Handle 11.5mm; Z Leadscrew; €5.59 Aliexpress; Anti-backlash nut; €1.69 Aliexpress; Lead 8mm; GT2 Pulley 40T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

Name Amount Price Link Note Total

Electronics €18.68

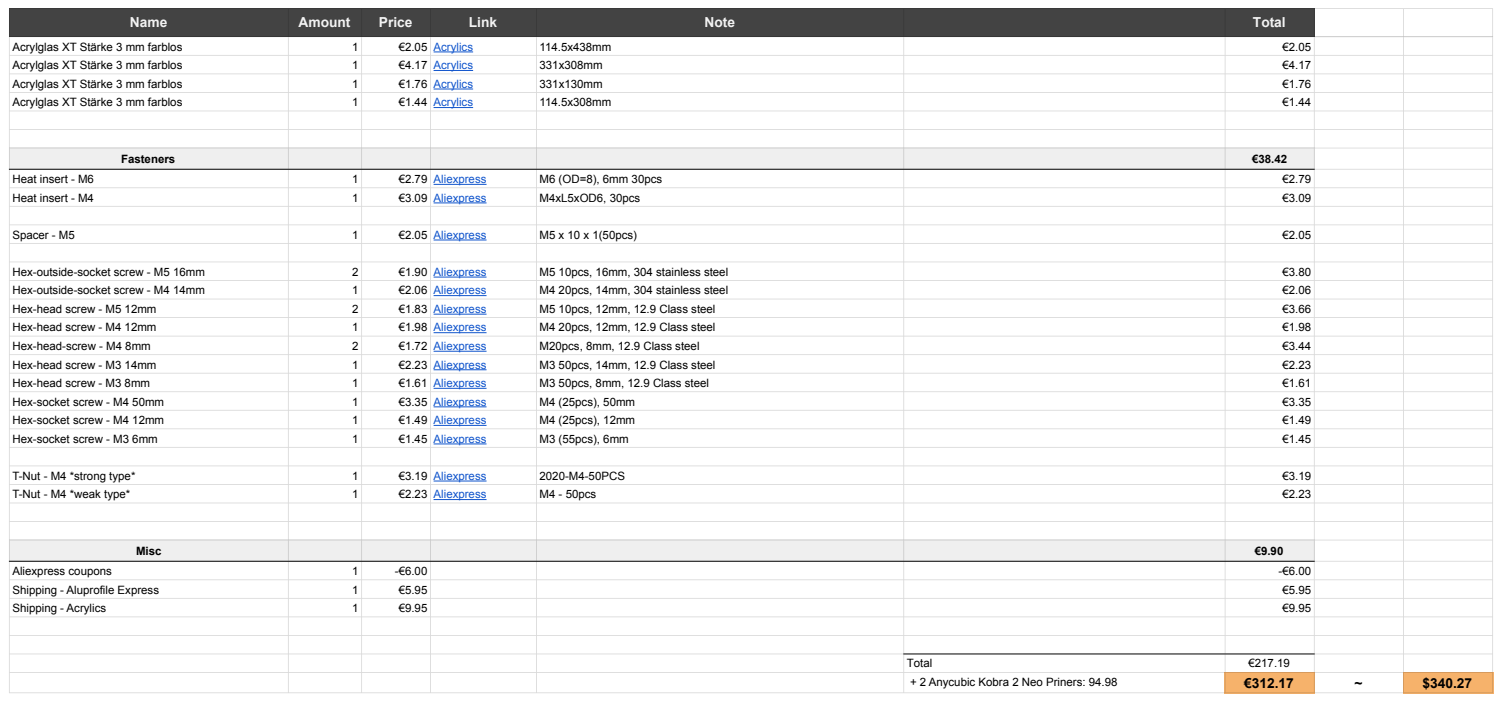
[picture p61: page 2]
Name; Amount; Price; Link; Note; Total; Acrylglas XT Stärke 3 mm farblos; €2.05 Acrylics; €4.17 Acrylics; €1.76 Acrylics; €1.44 Acrylics; Fasteners; Heat insert - M6; €2.79 Aliexpress; M6 (OD=8), 6mm 30pcs; Heat insert - M4; €3.09 Aliexpress; M4xL5xOD6, 30pcs; Spacer - M5; €2.05 Aliexpress; M5 x 10 x 1(50pcs); Hex-outside-socket screw - M5 16mm; €1.90 Aliexpress; M5 10pcs, 16mm, 304 stainless steel; Hex-outside-socket screw - M4 14mm; €2.06 Aliexpress; M4 20pcs, 14mm, 304 stainless steel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

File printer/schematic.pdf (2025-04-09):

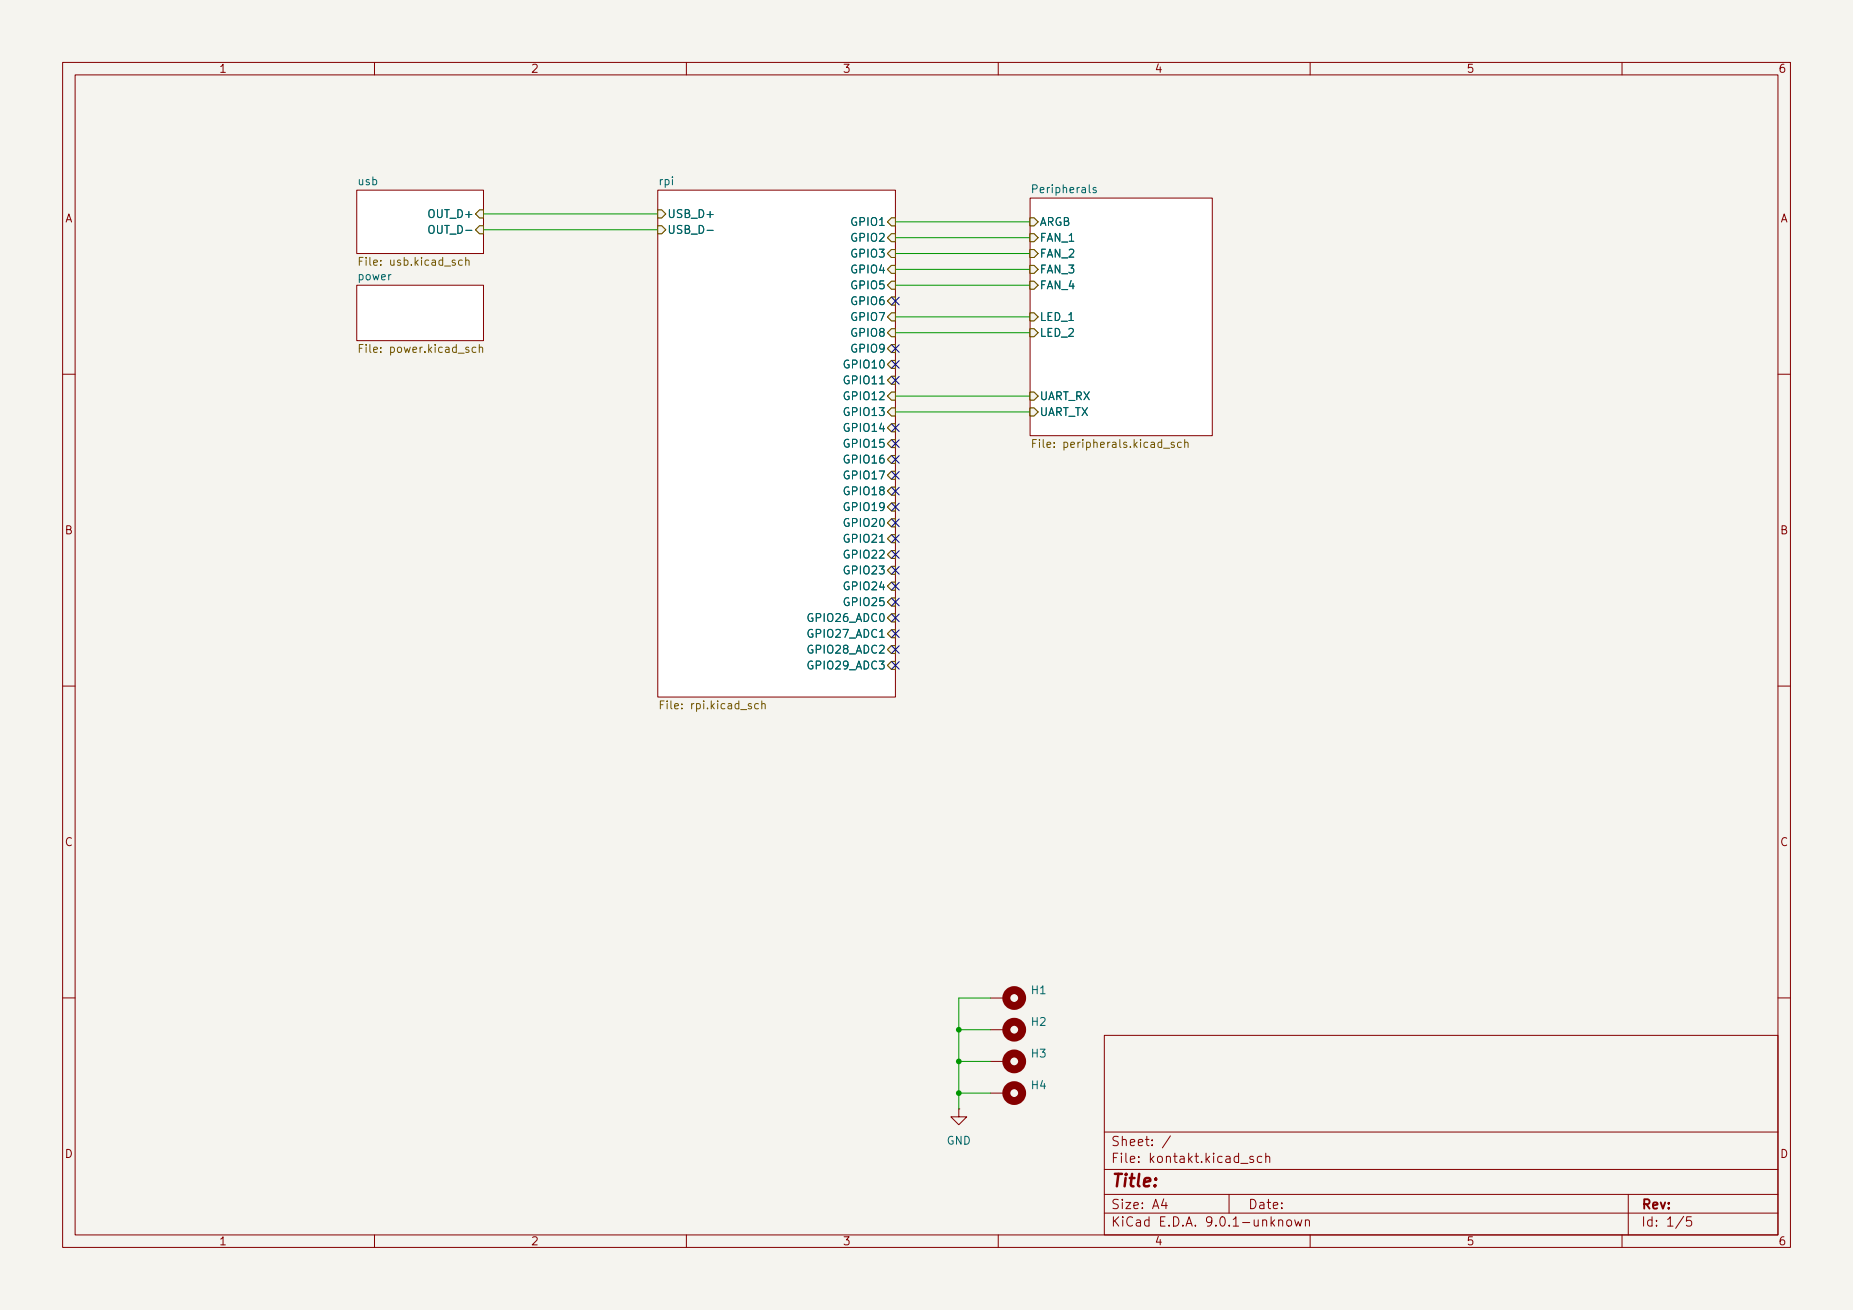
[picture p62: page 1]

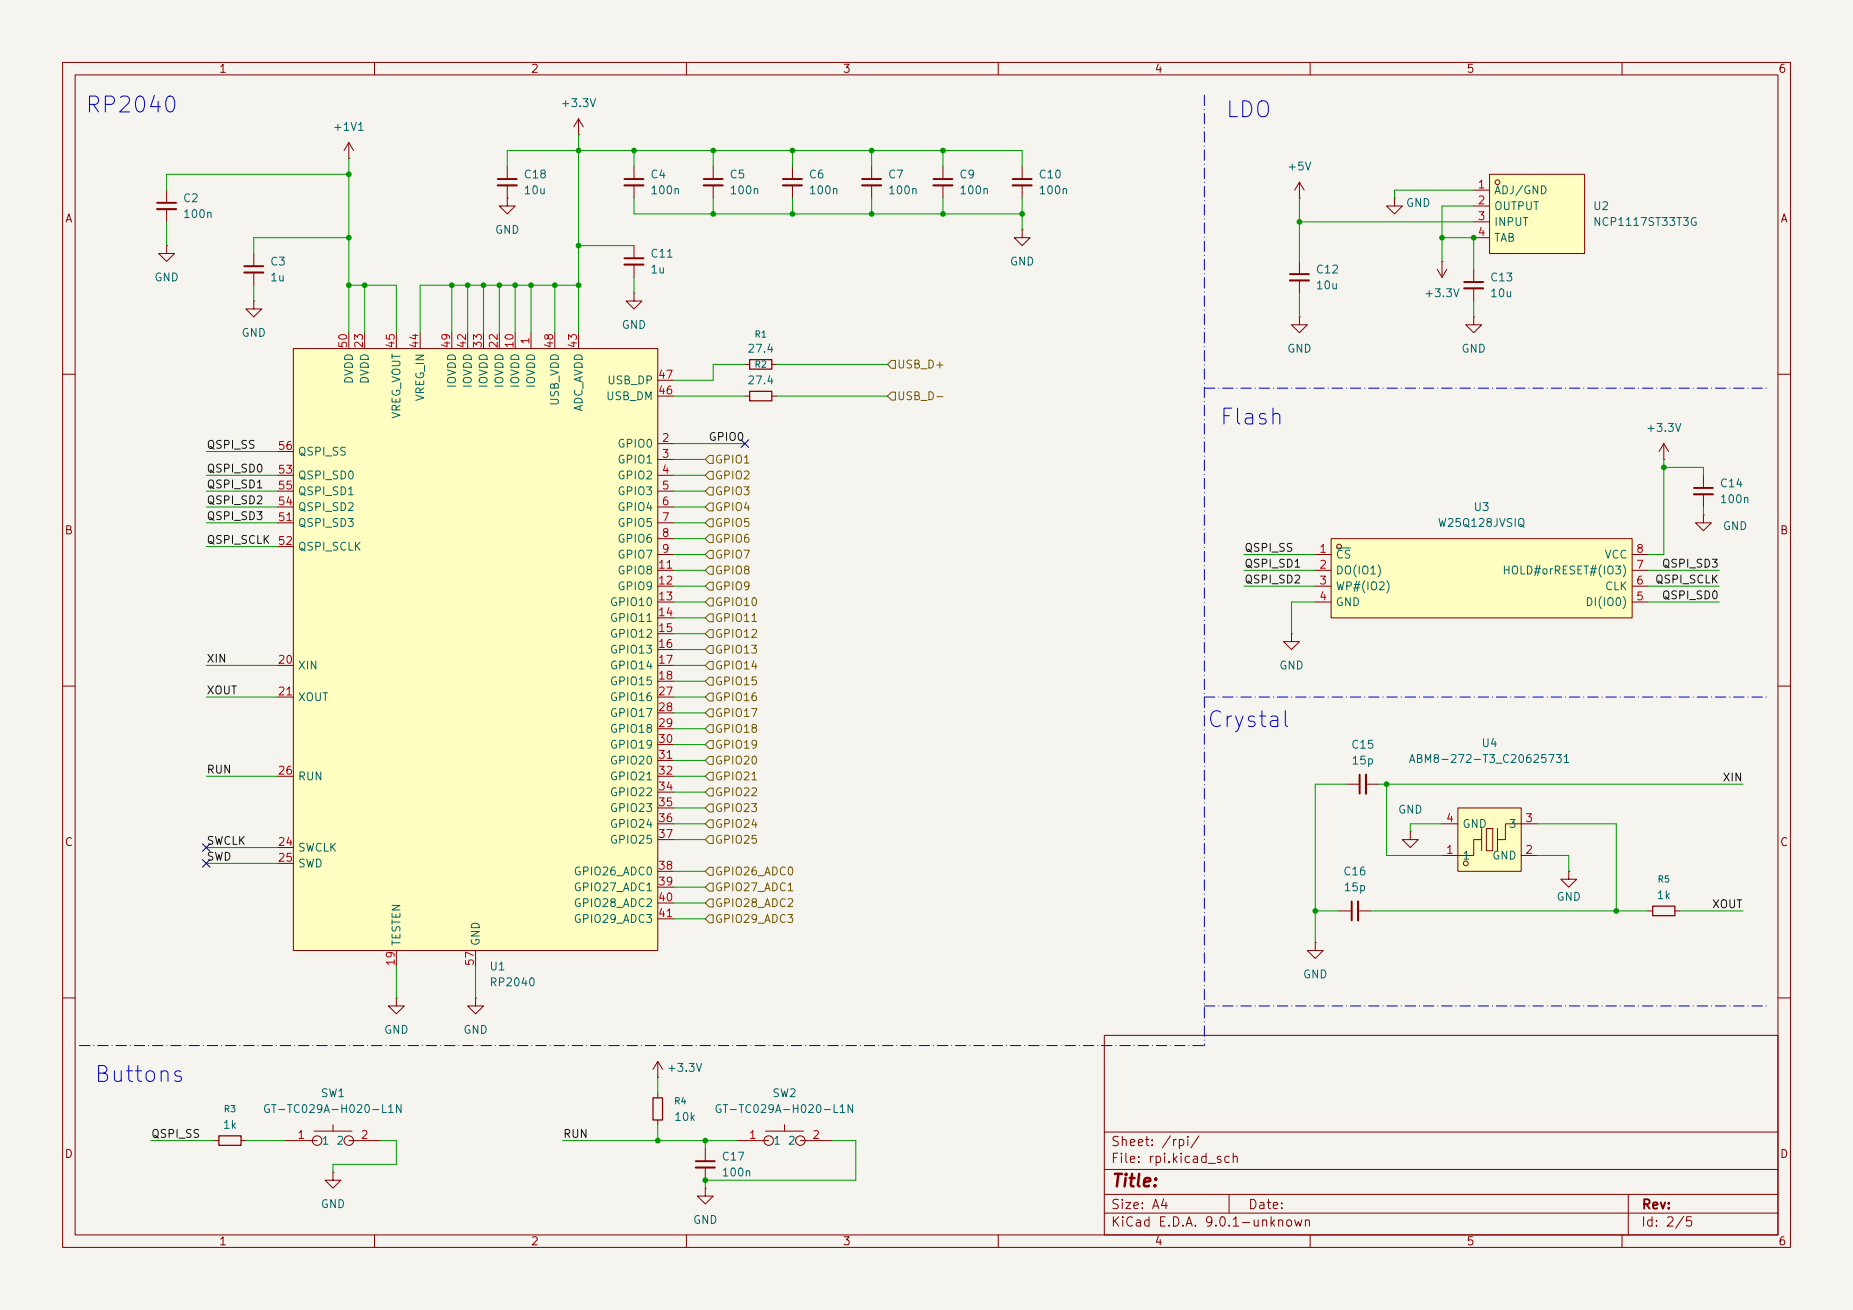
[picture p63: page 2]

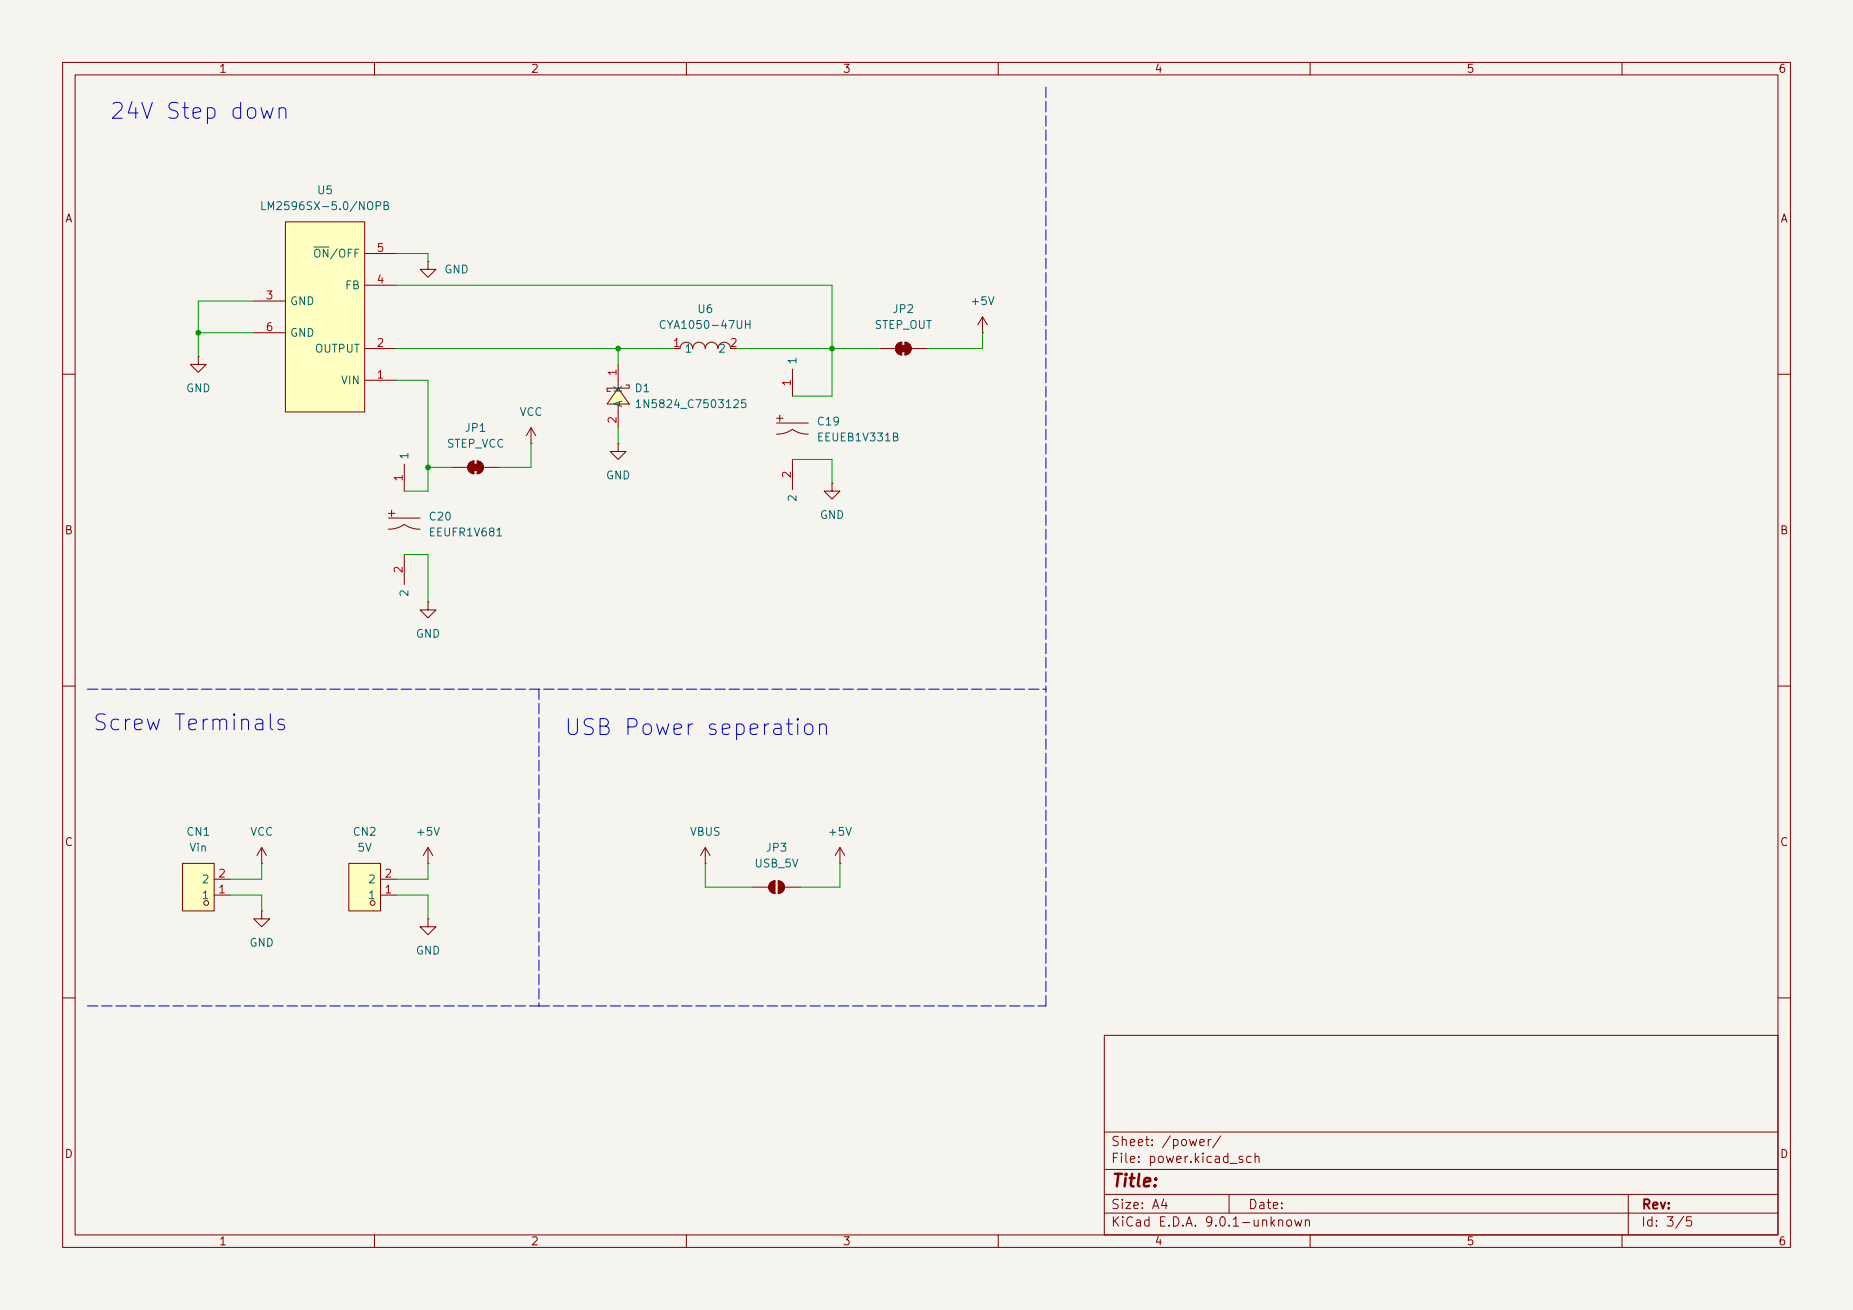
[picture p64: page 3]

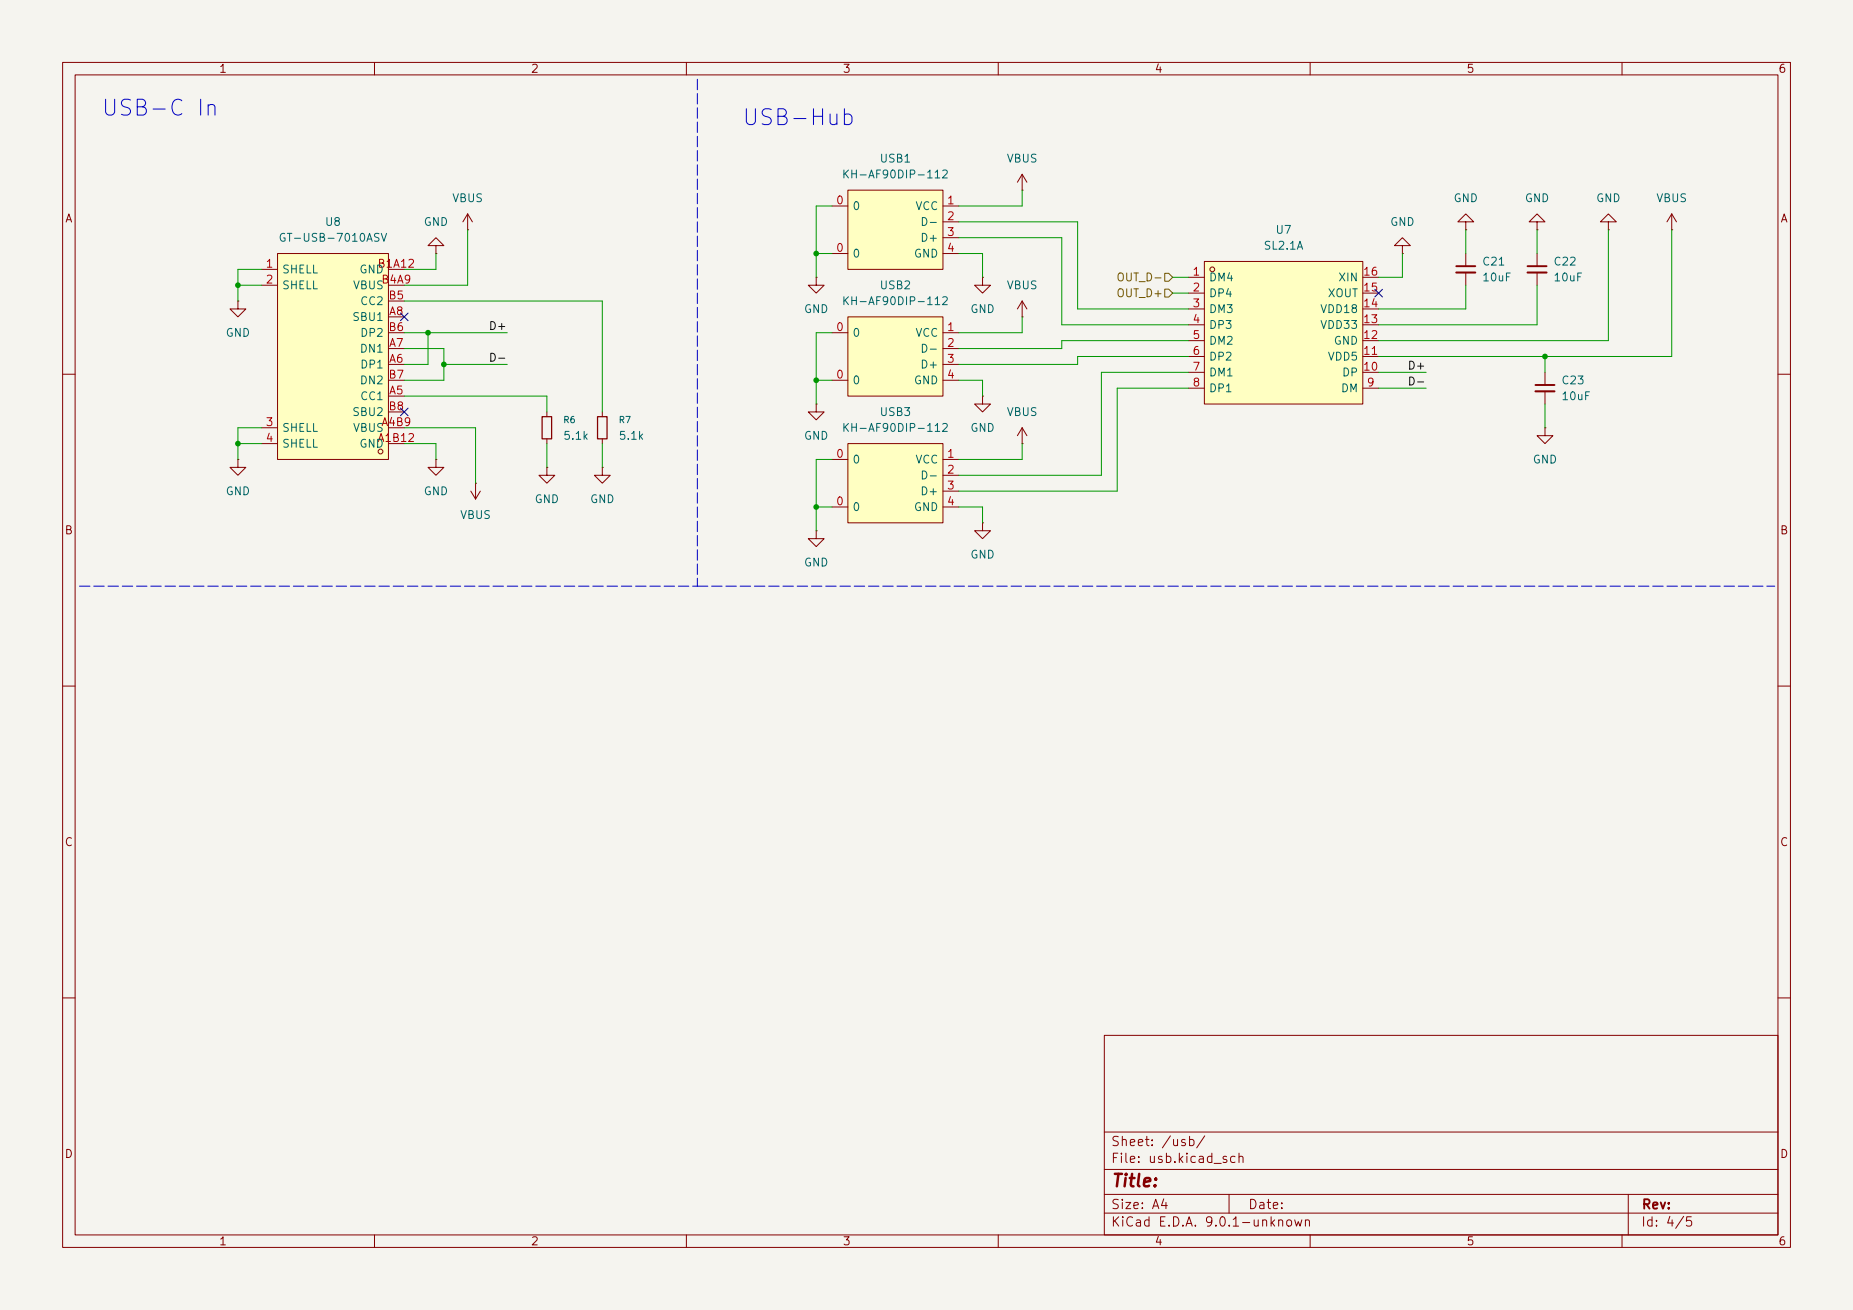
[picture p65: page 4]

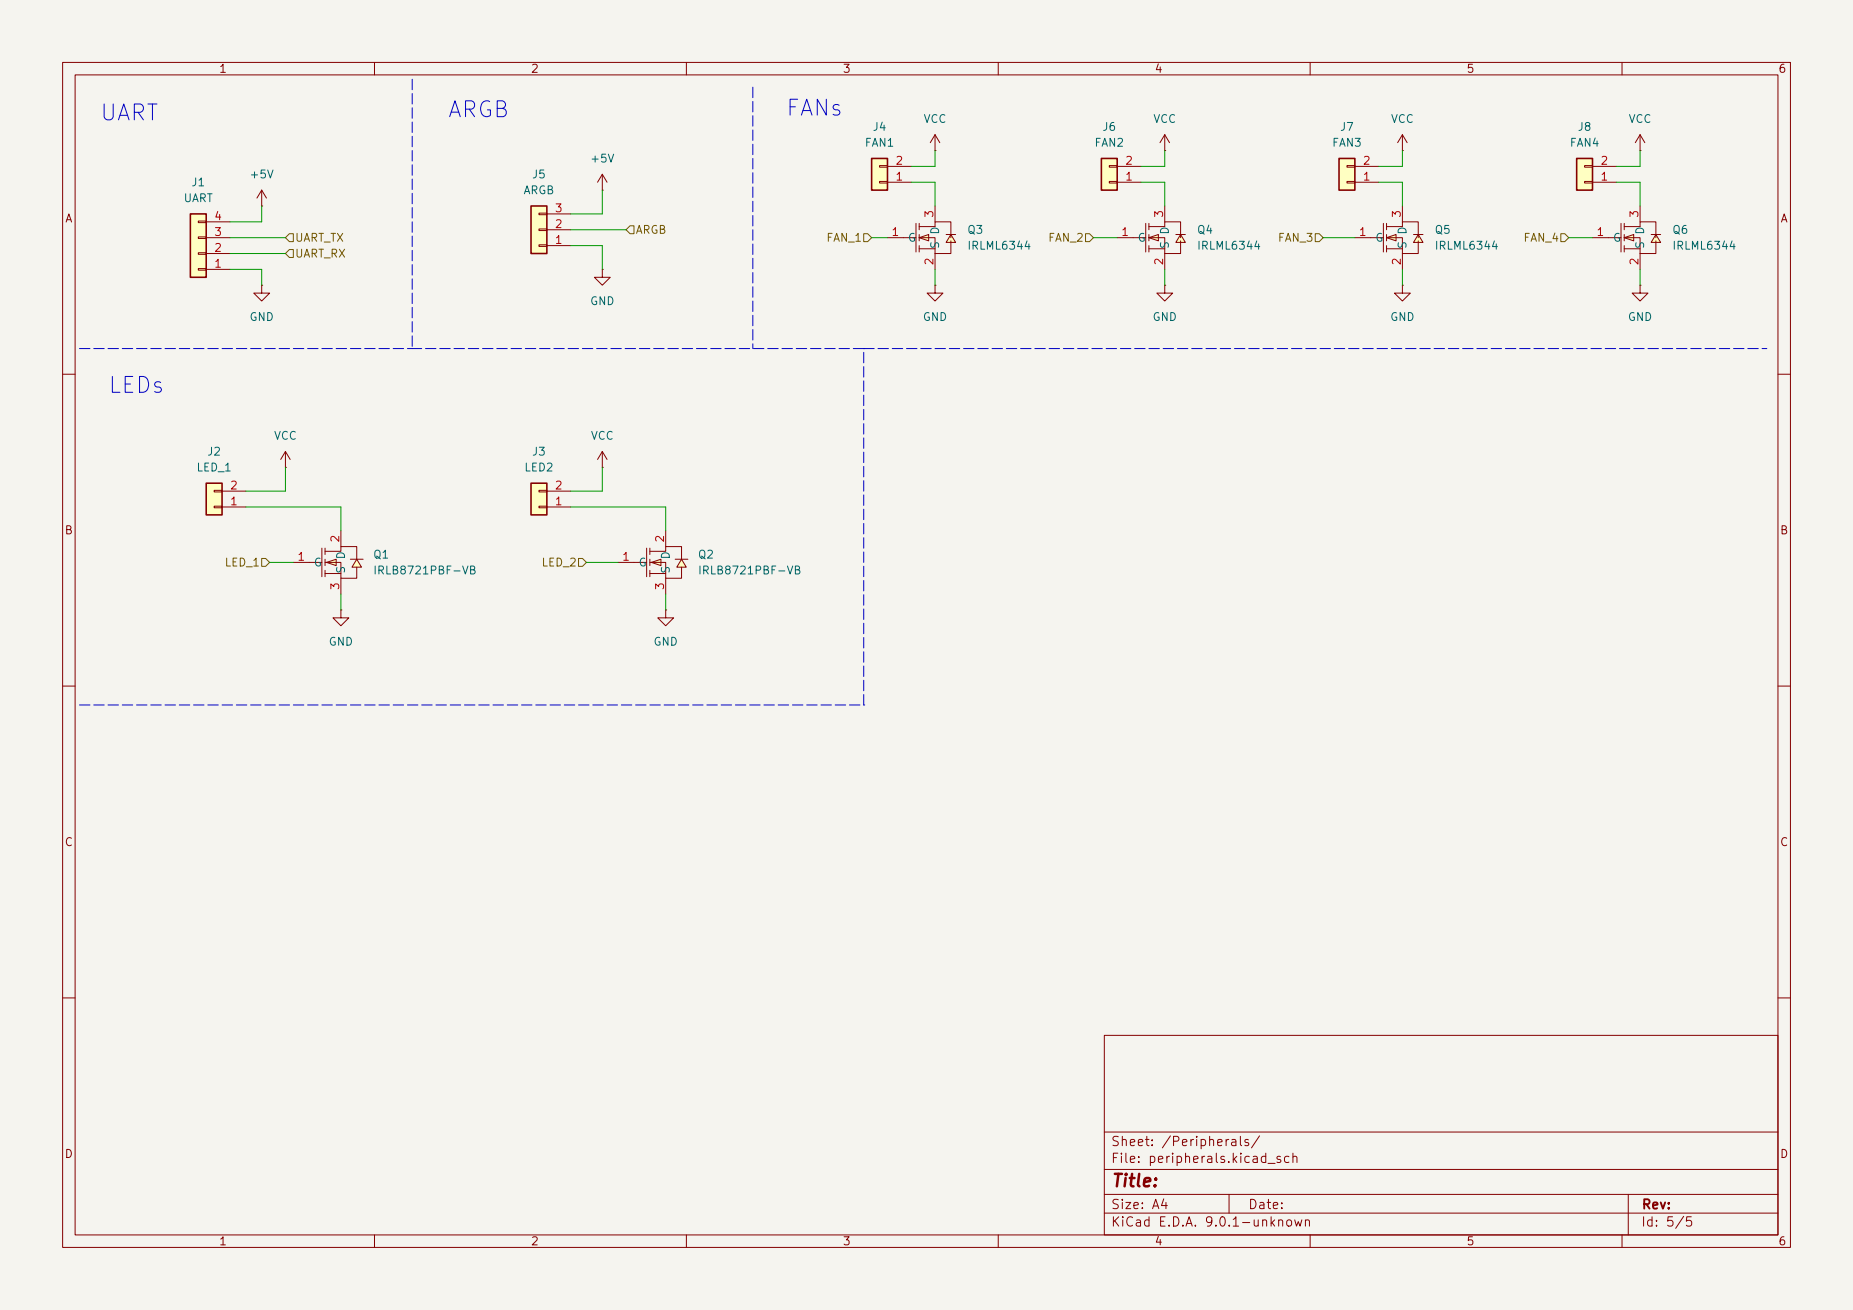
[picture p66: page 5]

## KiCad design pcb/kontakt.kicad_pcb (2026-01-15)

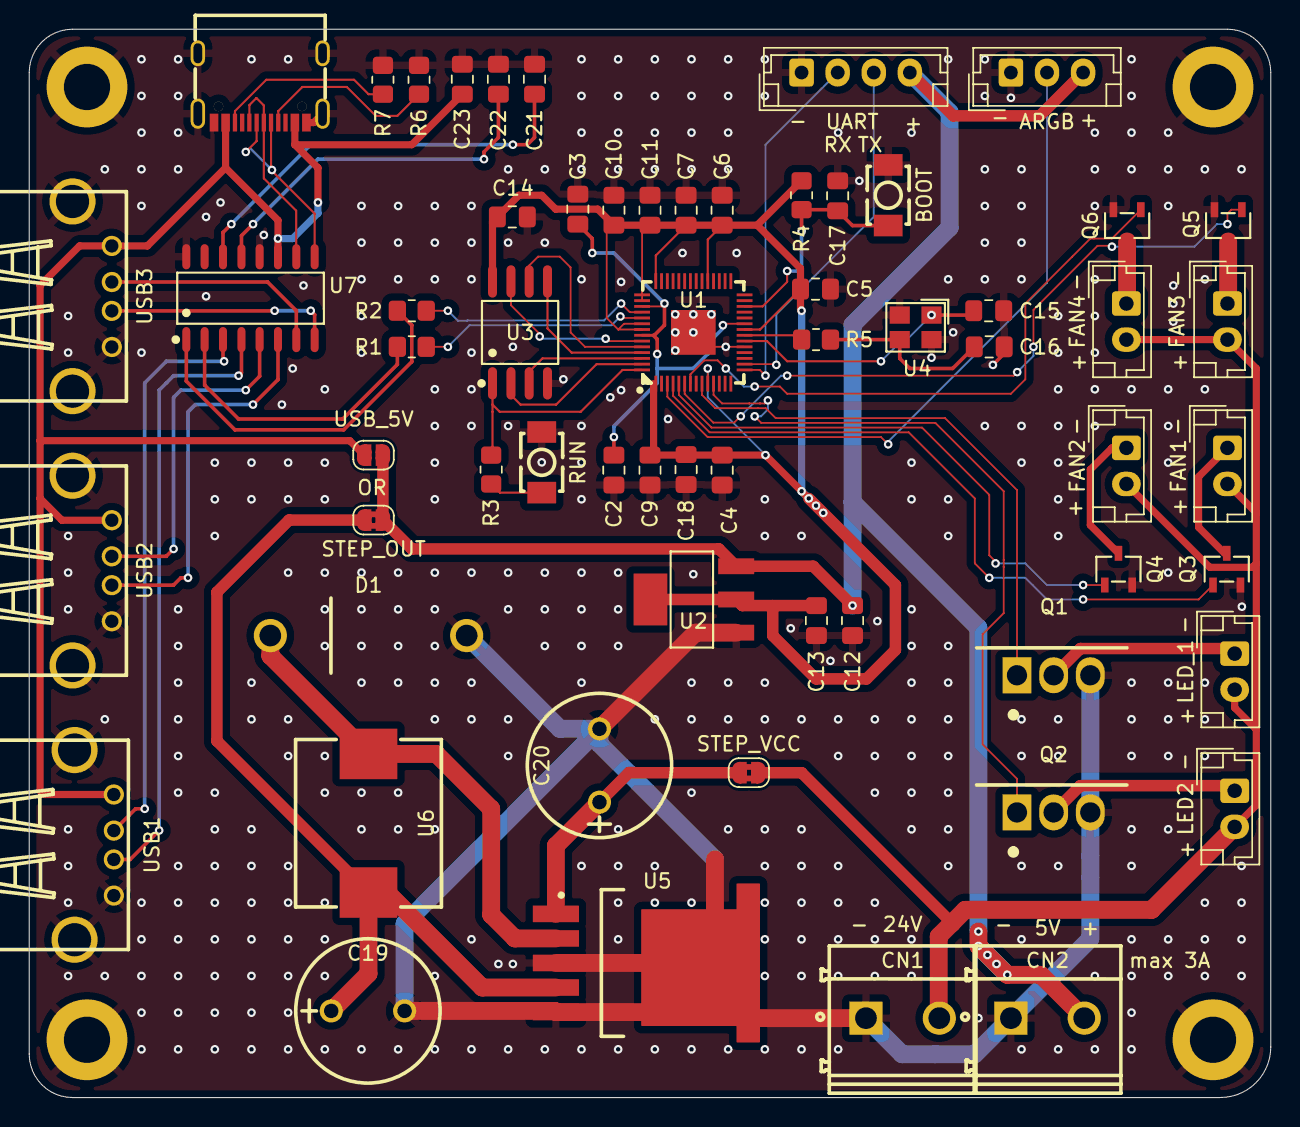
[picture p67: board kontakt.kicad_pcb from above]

Board: 2 copper layers, 86.0 x 74.0 mm, 65 parts (0 on the bottom side), 51 nets.

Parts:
C2, C4, C5, C6, C7, C9, C10, C14, C17: 100n; C_0805_2012Metric_Pad1.18x1.45mm_HandSolder
C3, C11: 1u; C_0805_2012Metric_Pad1.18x1.45mm_HandSolder
C12, C13, C18: 10u; C_0805_2012Metric_Pad1.18x1.45mm_HandSolder
C15, C16: 15p; C_0805_2012Metric_Pad1.18x1.45mm_HandSolder
C19: EEUEB1V331B; CAP-TH_BD10.0-P5.00-D1.0-FD
C20: EEUFR1V681; CAP-TH_BD10.0-P5.00-D1.0-FD
C21, C22, C23: 10uF; C_0805_2012Metric_Pad1.18x1.45mm_HandSolder
CN1: Vin; CONN-TH_2P-P5.08_DIBO_DB128V-5.08
CN2: 5V; CONN-TH_2P-P5.08_DIBO_DB128V-5.08
D1: 1N5824_C7503125; DO-27_BD5.3-L8.4-P12.40-D1.3-RD
H1, H2, H3, H4: MountingHole_Pad; MountingHole_3.2mm_M3_DIN965_Pad
J1: UART; JST_EH_B4B-EH-A_1x04_P2.50mm_Vertical
J2: LED_1; JST_EH_B2B-EH-A_1x02_P2.50mm_Vertical
J3: LED2; JST_EH_B2B-EH-A_1x02_P2.50mm_Vertical
J4: FAN1; JST_EH_B2B-EH-A_1x02_P2.50mm_Vertical
J5: ARGB; JST_EH_B3B-EH-A_1x03_P2.50mm_Vertical
J6: FAN2; JST_EH_B2B-EH-A_1x02_P2.50mm_Vertical
J7: FAN3; JST_EH_B2B-EH-A_1x02_P2.50mm_Vertical
J8: FAN4; JST_EH_B2B-EH-A_1x02_P2.50mm_Vertical
JP1: STEP_VCC; SolderJumper-2_P1.3mm_Bridged2Bar_RoundedPad1.0x1.5mm
JP2: STEP_OUT; SolderJumper-2_P1.3mm_Bridged2Bar_RoundedPad1.0x1.5mm
JP3: USB_5V; SolderJumper-2_P1.3mm_Open_RoundedPad1.0x1.5mm
Q1, Q2: IRLB8721PBF-VB; TO-220AB-3_L10.4-W4.6-P2.54-L
Q3, Q4, Q5, Q6: IRLML6344; SOT-23-3_L3.0-W1.7-P0.95-LS2.9-BR
R1, R2: 27.4; R_0805_2012Metric_Pad1.20x1.40mm_HandSolder
R3, R5: 1k; R_0805_2012Metric_Pad1.20x1.40mm_HandSolder
R4: 10k; R_0805_2012Metric_Pad1.20x1.40mm_HandSolder
R6, R7: 5.1k; R_0805_2012Metric_Pad1.20x1.40mm_HandSolder
SW1, SW2: GT-TC029A-H020-L1N; SW-SMD_L3.9-W2.9-LS5.0
U1: RP2040; LQFN-56_L7.0-W7.0-P0.4-EP
U2: NCP1117ST33T3G; SOT-223-3_L6.5-W3.4-P2.30-LS7.0-BR
U3: W25Q128JVSIQ; SOIC-8_L5.3-W5.3-P1.27-LS8.0-BL
U4: ABM8-272-T3_C20625731; CRYSTAL-SMD_4P-L3.2-W2.5-BL
U5: LM2596SX-5.0/NOPB; TO-263-5_L10.2-W8.9-P1.70-TL
U6: CYA1050-47UH; IND-SMD_L11.6-W10.1
U7: SL2.1A; SOP-16_L10.0-W3.9-P1.27-LS6.0-BL
U8: GT-USB-7010ASV; USB-C-SMD_G-SWITCH_GT-USB-7010ASV
USB1, USB2, USB3: KH-AF90DIP-112; USB-A-TH_USB-A-F-90

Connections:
+1V1: C2.1, C3.1, U1.23 (DVDD), U1.45 (VREG_VOUT), U1.50 (DVDD)
+3.3V: C4.1, C5.1, C6.1, C7.1, C9.1, C10.1, C11.1, C13.1, C14.1, C18.1, R4.2, U1.1 (IOVDD), U1.10 (IOVDD), U1.22 (IOVDD), U1.33 (IOVDD), U1.42 (IOVDD), U1.43 (ADC_AVDD), U1.44 (VREG_IN), U1.48 (USB_VDD), U1.49 (IOVDD), U2.2 (OUTPUT), U2.4 (TAB), U3.8 (VCC)
+5V: C12.1, CN2.2, J1.4, J5.3, JP2.2 (B), JP3.2 (B), U2.3 (INPUT)
/Peripherals/ARGB: J5.2, U1.3 (GPIO1)
/Peripherals/FAN_1: Q3.1 (G), U1.4 (GPIO2)
/Peripherals/FAN_2: Q4.1 (G), U1.5 (GPIO3)
/Peripherals/FAN_3: Q5.1 (G), U1.6 (GPIO4)
/Peripherals/FAN_4: Q6.1 (G), U1.7 (GPIO5)
/Peripherals/LED_1: Q1.1 (G), U1.9 (GPIO7)
/Peripherals/LED_2: Q2.1 (G), U1.11 (GPIO8)
/Peripherals/UART_RX: J1.2, U1.15 (GPIO12)
/Peripherals/UART_TX: J1.3, U1.16 (GPIO13)
/rpi/QSPI_SCLK: U1.52 (QSPI_SCLK), U3.6 (CLK)
/rpi/QSPI_SD0: U1.53 (QSPI_SD0), U3.5 (DI(IO0))
/rpi/QSPI_SD1: U1.55 (QSPI_SD1), U3.2 (DO(IO1))
/rpi/QSPI_SD2: U1.54 (QSPI_SD2), U3.3 (WP#(IO2))
/rpi/QSPI_SD3: U1.51 (QSPI_SD3), U3.7 (HOLD#orRESET#(IO3))
/rpi/QSPI_SS: R3.1, U1.56 (QSPI_SS), U3.1 (~CS)
/rpi/RUN: C17.1, R4.1, SW2.1, U1.26 (RUN)
/rpi/USB_D+: R1.2, U7.2 (DP4)
/rpi/USB_D-: R2.2, U7.1 (DM4)
/rpi/XIN: C15.2, U1.20 (XIN), U4.1
/rpi/XOUT: R5.2, U1.21 (XOUT)
/usb/D+: U7.10 (DP), U8.A6 (DP1), U8.B6 (DP2)
/usb/D-: U7.9 (DM), U8.A7 (DN1), U8.B7 (DN2)
GND: C2.2, C3.2, C4.2, C5.2, C6.2, C7.2, C9.2, C10.2, C11.2, C12.2, C13.2, C14.2, C15.1, C16.1, C17.2, C18.2, C19.2, C20.2, C21.1, C22.1, C23.2, CN1.1, CN2.1, D1.2 (A), H1.1, H2.1, H3.1, H4.1, J1.1, J5.1, Q1.3 (S), Q2.3 (S), Q3.2 (S), Q4.2 (S), Q5.2 (S), Q6.2 (S), R6.2, R7.2, SW1.2, SW2.2, U1.19 (TESTEN), U1.57 (GND), U2.1 (ADJ/GND), U3.4 (GND), U4.2 (GND), U4.4 (GND), U5.3 (GND), U5.5 (~ON/OFF), U5.6 (GND), U7.12 (GND), U7.16 (XIN), U8.1 (SHELL), U8.2 (SHELL), U8.3 (SHELL), U8.4 (SHELL), U8.A1B12 (GND), U8.B1A12 (GND), USB1.0, USB1.4 (GND), USB2.0, USB2.4 (GND), USB3.0, USB3.4 (GND)
unnamed: C16.2, R5.1, U4.3
unnamed: D1.1 (K), U5.2 (OUTPUT), U6.1
unnamed: J2.1, Q1.2 (D)
unnamed: J3.1, Q2.2 (D)
unnamed: J4.1, Q3.3 (D)
unnamed: J6.1, Q4.3 (D)
unnamed: J7.1, Q5.3 (D)
unnamed: J8.1, Q6.3 (D)
unnamed: C20.1, JP1.1 (A), U5.1 (VIN)
unnamed: C19.1, JP2.1 (A), U5.4 (FB), U6.2
unnamed: R3.2, SW1.1
unnamed: R2.1, U1.46 (USB_DM)
unnamed: R1.1, U1.47 (USB_DP)
unnamed: U7.7 (DM1), USB3.2 (D-)
unnamed: U7.5 (DM2), USB2.2 (D-)
unnamed: U7.3 (DM3), USB1.2 (D-)
unnamed: U7.8 (DP1), USB3.3 (D+)
unnamed: U7.6 (DP2), USB2.3 (D+)
unnamed: U7.4 (DP3), USB1.3 (D+)
unnamed: C21.2, U7.14 (VDD18)
unnamed: C22.2, U7.13 (VDD33)
unnamed: R6.1, U8.A5 (CC1)
unnamed: R7.1, U8.B5 (CC2)
VBUS: C23.1, JP3.1 (A), U7.11 (VDD5), U8.A4B9 (VBUS), U8.B4A9 (VBUS), USB1.1 (VCC), USB2.1 (VCC), USB3.1 (VCC)
VCC: CN1.2, J2.2, J3.2, J4.2, J6.2, J7.2, J8.2, JP1.2 (B)

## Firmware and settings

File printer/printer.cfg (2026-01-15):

[include mainsail.cfg]
# MCUs
[mcu] # Left one
serial: /dev/serial/by-path/platform-3f980000.usb-usb-0:1.4:1.0
restart_method: command

[mcu second] # Right one
serial: /dev/serial/by-path/platform-3f980000.usb-usb-0:1.1:1.0
restart_method: command

[temperature_sensor main_mcu_temp]
sensor_type: temperature_mcu
min_temp: 0
max_temp: 100

[temperature_sensor second_mcu_temp]
sensor_type: temperature_mcu
sensor_mcu: second
min_temp: 0
max_temp: 100

[temperature_sensor raspberry_pi]
sensor_type: temperature_host
min_temp: 10
max_temp: 100

# Meta
[printer]
kinematics: cartesian
max_velocity: 500
max_accel: 3000
max_z_velocity: 10
max_z_accel: 15

[neopixel main_rgb]
pin: gpio24
chain_count: 1
color_order: GRB
initial_RED: 0.0
initial_GREEN: 0.05
initial_BLUE: 0.0

[neopixel second_rgb]
pin: second:gpio24
chain_count: 1
color_order: GRB
initial_RED: 0.0
initial_GREEN: 0.0
initial_BLUE: 0.05

# Steppers

# X
[stepper_x]
step_pin: gpio11
dir_pin: !gpio10
enable_pin: !gpio12
rotation_distance: 40
microsteps: 32
full_steps_per_rotation: 200
endstop_pin: ^second:gpio25
position_endstop: -14
position_min: -14
position_max: 458
homing_speed: 40
homing_retract_dist: 0

[tmc2209 stepper_x]
uart_pin: gpio9
tx_pin: gpio8
uart_address: 0
run_current: 0.5
interpolate: False
sense_resistor: 0.110
stealthchop_threshold: 0


# Y Right
[stepper_y]
step_pin: gpio6
dir_pin: gpio5
enable_pin: !gpio7
rotation_distance: 40
microsteps: 32
full_steps_per_rotation: 200
endstop_pin: tmc2209_stepper_y:virtual_endstop
position_endstop: -5
position_min: -5
position_max: 220
homing_speed: 40
homing_retract_dist: 0

[tmc2209 stepper_y]
uart_pin: gpio9
tx_pin: gpio8
uart_address: 2
run_current: 0.4
interpolate: False
sense_resistor: 0.110
stealthchop_threshold: 0                                            # Set to 999999 to turn stealthchop on, and 0 to use spreadcycle
diag_pin: ^gpio3    												# YOU NEED TO JUMP THIS DIAG PIN ON YOUR BOARD FOR SENSORLESS HOMING TO WORK
driver_SGTHRS: 100

# Y Left
[stepper_y1]
step_pin: gpio19
dir_pin: !gpio28
enable_pin: !gpio2
rotation_distance: 40
microsteps: 32
endstop_pin: tmc2209_stepper_y1:virtual_endstop

[tmc2209 stepper_y1]
uart_pin: gpio9
tx_pin: gpio8
uart_address: 1
run_current: 0.4
interpolate: False
sense_resistor: 0.110
stealthchop_threshold: 0
diag_pin: ^gpio25    												# YOU NEED TO JUMP THIS DIAG PIN ON YOUR BOARD FOR SENSORLESS HOMING TO WORK
driver_SGTHRS: 100

# Z-Left
[stepper_z]
step_pin: second:gpio6
dir_pin: second:gpio5
enable_pin: !second:gpio7
rotation_distance: 4
microsteps: 32
full_steps_per_rotation: 200
endstop_pin: probe:z_virtual_endstop
position_max: 200
position_min: -2

[tmc2209 stepper_z]
uart_pin: second:gpio9
tx_pin: second:gpio8
uart_address: 2
run_current: 0.4
interpolate: False
sense_resistor: 0.110
stealthchop_threshold: 0

# Z-Right
[stepper_z1]
step_pin: second:gpio19
dir_pin: !second:gpio28
enable_pin: !second:gpio2
rotation_distance: 4
microsteps: 32


[tmc2209 stepper_z1]
uart_pin: second:gpio9
tx_pin: second:gpio8
uart_address: 1
run_current: 0.4
interpolate: False
sense_resistor: 0.110
stealthchop_threshold: 0

# Extruder
[extruder]
step_pin: gpio14
dir_pin: !gpio13
enable_pin: !gpio15
full_steps_per_rotation: 200
microsteps: 32
max_extrude_only_distance: 200
rotation_distance: 7.084
nozzle_diameter: 0.400
filament_diameter: 1.750
pressure_advance: 0.06
heater_pin: second:gpio23
sensor_type: ATC Semitec 104GT-2
sensor_pin: second:gpio27
#control: pid
#pid_ki: 0.88
#pid_kd: 59.12
#pid_kp: 14.42
min_temp: 0
max_temp: 240
min_extrude_temp: 170
max_extrude_cross_section: 4

[tmc2209 extruder]
uart_pin: gpio9
tx_pin: gpio8
uart_address: 3
run_current: 0.6
interpolate: False
sense_resistor: 0.110
stealthchop_threshold: 0

# Beds
[heater_bed]
heater_pin: gpio21
sensor_type: EPCOS 100K B57560G104F
sensor_pin: gpio26
smooth_time: 3.0
min_temp: 0
max_temp: 120
control: pid
pid_kp: 97.1 #tune this with this guide (https://www.obico.io/blog/klipper-pid-tuning/)
pid_ki: 1.41
pid_kd: 1675.16

[heater_generic second]
gcode_id: second
heater_pin: second:gpio21
sensor_type: EPCOS 100K B57560G104F
sensor_pin: second:gpio26
smooth_time: 3.0
min_temp: 0
max_temp: 120
#control: pid
#pid_kp: 97.1 #tune this with this guide (https://www.obico.io/blog/klipper-pid-tuning/)
#pid_ki: 1.41
#pid_kd: 1675.16

# Fans
[heater_fan hotend_fan]
pin: second:gpio17
max_power: 1.0
kick_start_time: 0.5
heater: extruder
heater_temp: 50.0
cycle_time: 0.010
off_below: 0.13

[fan]
pin: second:gpio18
max_power: 1.0
kick_start_time: 0.5
off_below: 0.13
cycle_time: 0.010

# Probe
[probe]
pin: ^second:gpio22
x_offset: 0.0
y_offset: -24.0
#z_offset: 5.0
#speed: 5.0
#   Speed (in mm/s) of the Z axis when probing. The default is 5mm/s.
samples: 3
#   The number of times to probe each point. The probed z-values will
#   be averaged. The default is to probe 1 time.
#sample_retract_dist: 2.0
#   The distance (in mm) to lift the toolhead between each sample (if
#   sampling more than once). The default is 2mm.
#lift_speed:
#   Speed (in mm/s) of the Z axis when lifting the probe between
#   samples. The default is to use the same value as the 'speed'
#   parameter.
samples_result: average
#   The calculation method when sampling more than once - either
#   "median" or "average". The default is average.
samples_tolerance: 0.100
#   The maximum Z distance (in mm) that a sample may differ from other
#   samples. If this tolerance is exceeded then either an error is
#   reported or the attempt is restarted (see
#   samples_tolerance_retries). The default is 0.100mm.
samples_tolerance_retries: 1
#   The number of times to retry if a sample is found that exceeds
#   samples_tolerance. On a retry, all current samples are discarded
#   and the probe attempt is restarted. If a valid set of samples are
#   not obtained in the given number of retries then an error is
#   reported. The default is zero which causes an error to be reported
#   on the first sample that exceeds samples_tolerance.

[safe_z_home]
home_xy_position: 100.0, 100.0
speed: 50.0
z_hop: 2
z_hop_speed: 15.0
move_to_previous: False

# Z-Tilt
[z_tilt]
z_positions: 20, 110
  440, 110
points: 20, 110
  440, 110
speed: 150
horizontal_move_z: 10
retries: 6
retry_tolerance: 0.025

# Bed level adjust
[screws_tilt_adjust] # Use with SCREWS_TILT_CALCULATE
screw1: 35, 70
screw1_name: L_FL
screw2: 35, 220
screw2_name: L_BL
screw3: 195, 70
screw3_name: L_FR
screw4: 195, 220
screw4_name: L_BR

screw5: 265, 70
screw5_name: R_FL
screw6: 265, 220
screw6_name: R_BL
screw7: 425, 70
screw7_name: R_FR
screw8: 425, 220
screw8_name: R_BR

speed: 150
horizontal_move_z: 10
screw_thread: CW-M4

# Bed mesh
[bed_mesh]
speed: 200
horizontal_move_z: 7
mesh_min: 10, 20
mesh_max: 440, 190
probe_count: 20, 10
move_check_distance: 5
split_delta_z: .025
algorithm: bicubic
scan_overshoot: 5

# Random
[virtual_sdcard]
path: /home/playlogo/printer_data/gcodes
on_error_gcode: CANCEL_PRINT

[force_move]
enable_force_move: True

[exclude_object]

[pause_resume]

[gcode_arcs]
resolution: 1.0
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

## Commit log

2025-04-07 started working on docs
    [bom.xlsx]
2025-04-08 Improved docs, updated bom
    [bom.xlsx]
2025-04-08 Improved docs!
    [bom.xlsx]
2025-04-09 Added pcb!
    [bom.csv, designators.csv, kontakt.kicad_pcb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]
2025-04-10 Improved PCB docs
    [kontakt.kicad_pcb]
2025-07-17 Updated journal for finished printer
    [2x-Frame-Stepper-Mount.stl, 4x-TPU-Feet.stl, 4x-Z-Leadscrew-Spacer.stl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]
2025-07-19 Fixed image links in pcb readme
2026-01-14 Improved Kontakt PCB
    [kontakt.kicad_pcb]
2026-01-25 Added case for pcb
    [case_bottom.stl, case_top.stl, kontakt.kicad_sch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]
